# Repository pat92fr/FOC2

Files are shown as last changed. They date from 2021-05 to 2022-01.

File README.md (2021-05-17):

# Development repository for Smart Brushless Servo 

PID/FOC Custom Firmware for B-G431B-ESC1 board.

Follow us on Hackaday.io : https://hackaday.io/project/177578-b-g431b-esc-brushless-servo-controller

## Characteristics

- [x] 16KHz motor PWM 
- [x] Open-loop and closed-loop FOC algorithm (16KHz)
- [x] FOC with CSVPWM algorithm 
- [ ] FOC with Field-Weakening (work in progress)
- [x] Torque and Flux control (P only), with current limiter
- [x] Position control with min/max position limiter (4KHz)
- [x] Velocity control with max velocity limiter (4KHz) 
- [x] Torque and Flux feed-forward
- [x] Auto-calibration of electrical angle and motor rotation 
- [x] USB control interface : dynamixel like protocol allowing full-access to control (RAM) and configuration (EERPOM) 
- [x] CAN control interface : variable-size control frames (RX) and feedback frames (TX), with fail-safe on bus time-out
- [x] Power supply voltage monitoring, with min/max operating voltage (user configurable)
- [x] Position sensor monitoring, with fail-safe on system error and bus time-out
- [x] Temperature monitoring, with fail-safe on maximum temprature (user configurable) 
- [x] GUI Tool for configuration and test

# 1. Hardware (commercial off the shelf)

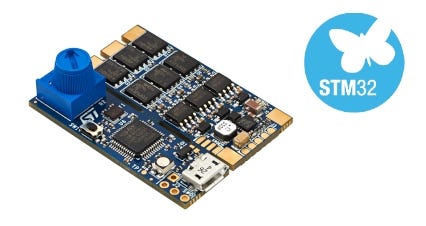
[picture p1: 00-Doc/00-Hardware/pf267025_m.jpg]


Product page : https://www.st.com/en/evaluation-tools/b-g431b-esc1.html

Cost: approx. 18$ per unit.

# 2. Wiring

As mentioned in the user manual, the B-G431B-ESC1 Discovery kit is equipped with a USB connector and different pads for communication, such as:
* U4 USB port for programming and debugging
* J1 for CAN port
* J2 for SWD-STM32F103 (reserved)
* J3 for PWM/UART/BECout input/output signal
* J4 for SWD-STM32G431 debug/programming port (without daughterboard)
* J5/J6 for Lipo battery (30V or 6S max)
* J7 for motor
* J8 for motor sensor (Hall or encoder)

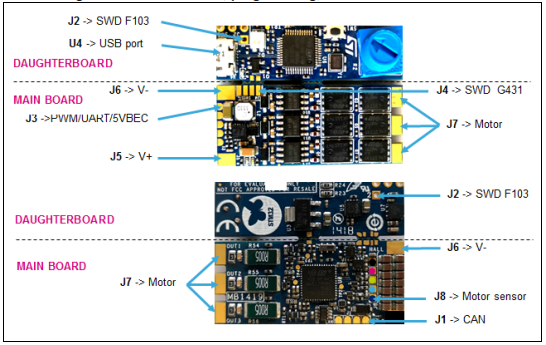
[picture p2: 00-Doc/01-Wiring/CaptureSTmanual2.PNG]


The USB interface is provided on the daughterboard and it allows to program and debug the main board. It provides also the supply voltage to the STM32G431CB MCU in case of no voltage on the bus (J5 and J6 not connected to the LiPo battery).

**For proper operation of the FOC firmware, the J1, J5, J6, J7, an J8 solder pads should be connected.**
The J2, J3, J4 solder pads may be left unconnected.

For J8, the firmware accept two types of position sensor :
* The AS5600 Position Sensor connected through I2C port (https://ams.com/as5600)
* The AS5048A High-Resolution Position Sensor connected through PWM interface (https://ams.com/as5048a)

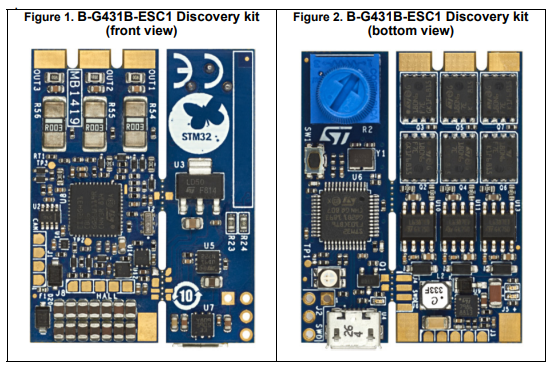
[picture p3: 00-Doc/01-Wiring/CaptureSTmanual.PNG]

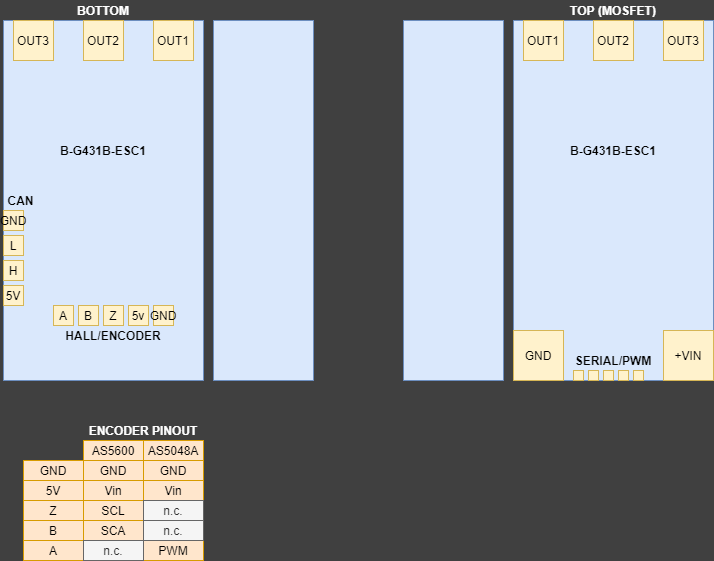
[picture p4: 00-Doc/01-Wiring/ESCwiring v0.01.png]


# 3. Uploading firmware

A full erase of the Chip is strongly recommended, to insure proper initialisation of the default configuration (the last Flash page stores PID/FOC configuration).

The release configuration of the PID/FOC firmware should be built with CubeIDE, and then uploaded using the USB port of the board.

**A hard-coded setting must be adjusted by user, according its hardware configuration :**

At lines 40+ of **main.c**, 
```
// Position sensor type :
//    "AS5600_I2C"
//    "AS5048A_PWM"
#define SENSOR_TYPE AS5048A_PWM
```
# 4. Local user interface

## 4.1. Red STATUS LED

The Red STATUS LED is normally OFF.

When an hardware error occurs, the LED is ON.

User may set the LED ON through USB interface.

## 4.2. Button

A short press on the button starts the calibration sequence. It last a few seconds and the motor turns slowly. Rotor should be free to get a good calibration.

***Notice : The number of pole pairs should be configured before starting the calibration sequence. User may set the pole pairs by connecting the ESC to a computer through USB and running the GUI tool.***

# 5. CAN protocol

The controller accepts CAN frame identifier = 000h + its own ID (user configurable ID).

The controler repies with CAN frame identifier = 010h + its own ID (user configurable ID).

## 5.1. Control frame formats

At ***start-up*** (power-on reset), the controller is in IDLE state (motor brake). The position and velocity set-points, the current feed-forward and the Kp and Kd are reset (=0).

In order to ***arm*** the controller, a full control frame with a 0xFFFFFFFFFFFFFFFF payload should be sent. The velocity set-point, the current feed-forward and the Kp and Kd are reset (=0). The position set-point is set to the present rotor position.

To ***disarm*** the controller, a full control frame with a 0x000000000000000 payload should be send. The position and velocity set-points, the current feed-forward and the Kp and Kd are reset (=0).

The controller ***disarms it-self*** automatically, when a CAN bus time-out occur (no control frame received for one second). The position and velocity set-points, the current feed-forward and the Kp and Kd are reset (=0).

For 16-bit fields, low byte first position, high byte second position.

### 5.1.1. Full control frame

A full control frame has a 64-bit payload.

Field | Length | Value
------------ | ------------- | -------------
Position | 16b | Position set-point in 1/10 degrees
Velocity | 16b | Velocity set-point in degrees per second
Torque | 16b | Torque current feed-forward in mA
Kp | 8b | Position control
Kd | 8b | Velocity control

***Warning : A high value of Kp or Kd may damage the actuator.***

### 5.1.2. Shortened control frames

A 48-bit control frame contains :

Field | Length | Value
------------ | ------------- | -------------
Position | 16b | Position set-point in 1/10 degrees
Velocity | 16b | Velocity set-point in degrees per second
Kp | 8b | Position control
Kd | 8b | Velocity control

A 32-bit control frame contains :

Field | Length | Value
------------ | ------------- | -------------
Position | 16b | Position set-point in 1/10 degrees
Velocity | 16b | Velocity set-point in degrees per second

A 16-bit control frame contains :

Field | Length | Value
------------ | ------------- | -------------
Torque | 16b | Torque current feed-forward in mA

## 5.2. Feedback frame formats

A 32-bit feedback frame contains :

Field | Length | Value
------------ | ------------- | -------------
Position | 16b | Present position in 1/10 degrees
Torque | 16b | Present torque current in mA

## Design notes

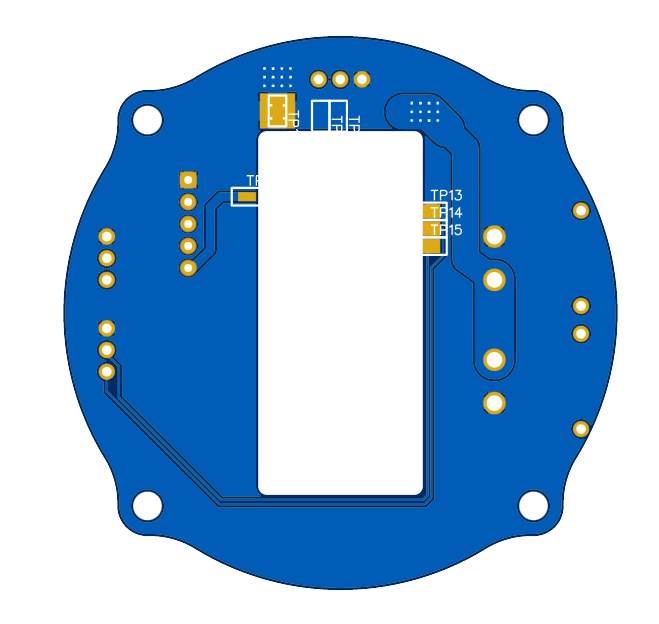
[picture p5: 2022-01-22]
03-Hardware/B-G431B-ESC1/bottom4.PNG

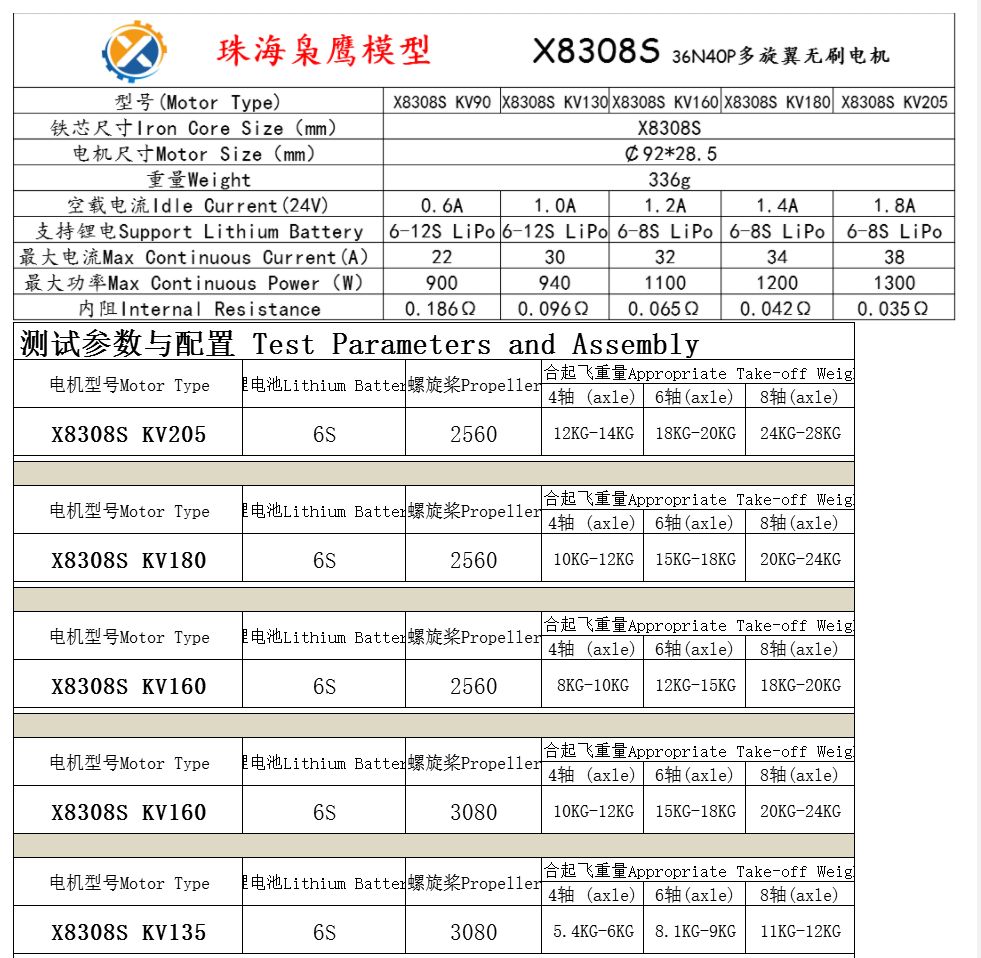
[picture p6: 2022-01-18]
03-Hardware/x8308s/Capture.PNG

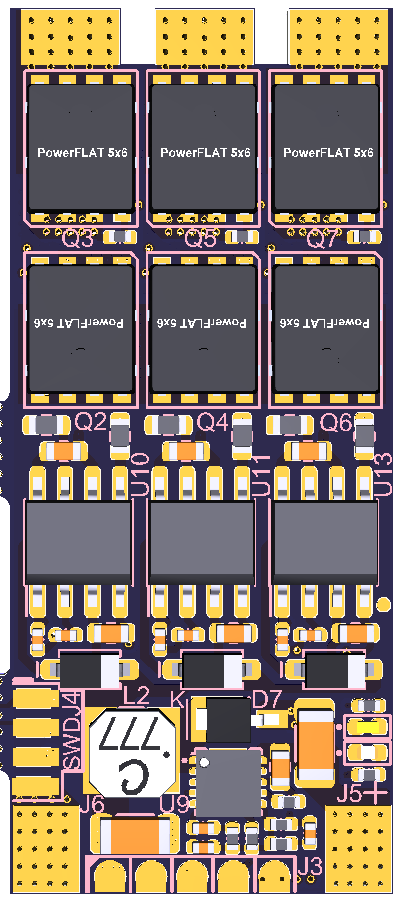
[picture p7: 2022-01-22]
03-Hardware/B-G431B-ESC1/Btop.PNG

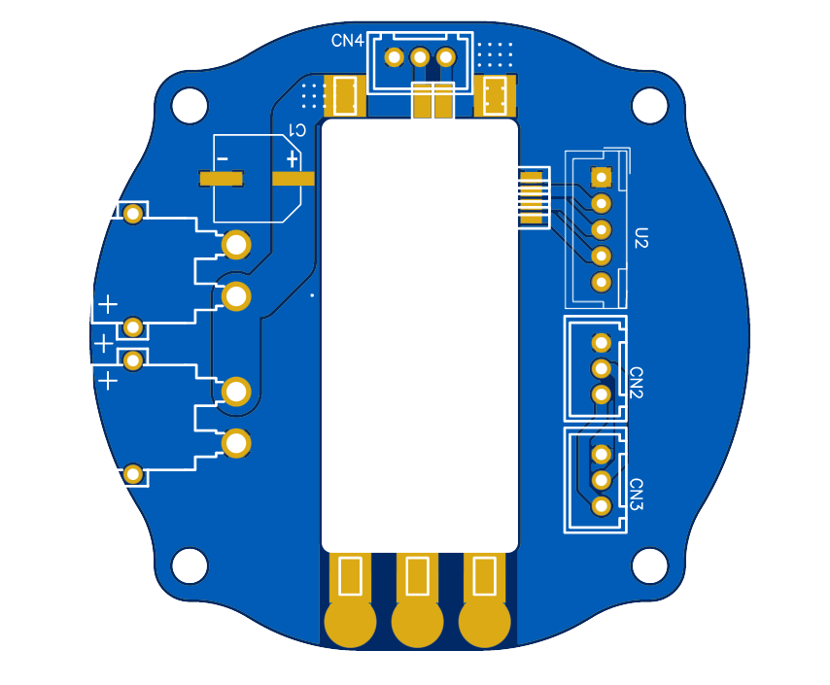
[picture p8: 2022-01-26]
03-Hardware/B-G431B-ESC1/board12.png

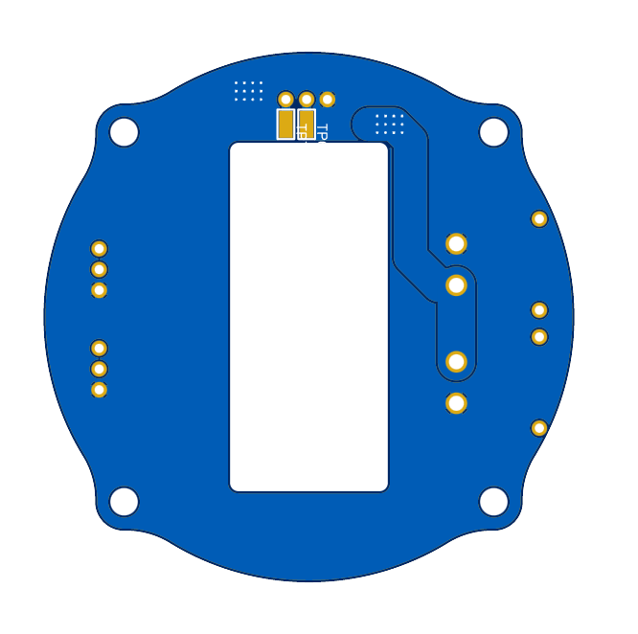
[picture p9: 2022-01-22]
03-Hardware/B-G431B-ESC1/bottom2.PNG

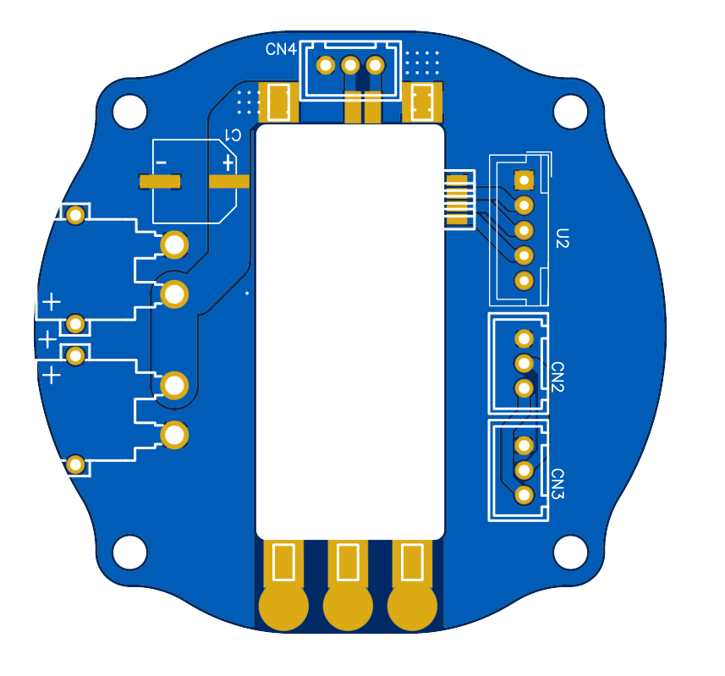
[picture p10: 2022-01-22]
03-Hardware/B-G431B-ESC1/board11.png

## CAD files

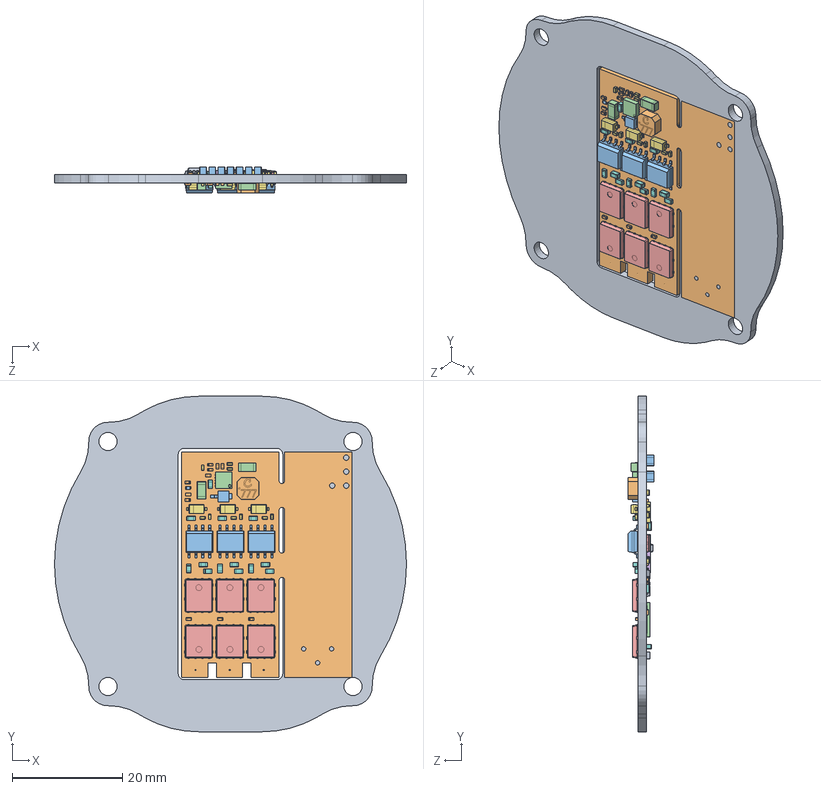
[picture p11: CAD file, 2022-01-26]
03-Hardware/B-G431B-ESC1/Assemblage.SLDASM
64.0 x 61.0 x 4.76 mm
Motherboard
CAPC2012X140 x 14
SON50P300X300X100-11
PowerFLAT_5x6 x 6
INDC1005X55
QFN6 x 2
SON40P120X100X55-6
SOT238
0435.250KRS
User_Library-LED_1006_G_Cut006
User_Library-LED_1006_G_Cut005
User_Library-LED_1006_G_Cut005_(Mirror_#1)
User_Library-LED_1006_G_Pad001
C281-1
C281-2
C281-3
C281-4
C281-5
C281-6
C281-7
SOD123 x 3
CAPC1608X90 x 11
SODFL1608X65 x 10
LPS4018
DO-216AA
CAPC3216X127 x 2
CSTCE
QFN48_7x7
CAPC1005X55 x 28
RESC1608X50 x 9
RESC2012X70 x 3
RESC1005 x 42
SOIC127P600X175 x 3
RESC6330 x 3
pcb_cut

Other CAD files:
03-Hardware/B-G431B-ESC1/C5.sldasm
03-Hardware/B-G431B-ESC1/R63.sldasm
03-Hardware/B-G431B-ESC1/C11.sldasm
03-Hardware/B-G431B-ESC1/D12.sldasm
03-Hardware/B-G431B-ESC1/R11.sldasm
03-Hardware/B-G431B-ESC1/D2.sldasm
03-Hardware/B-G431B-ESC1/Q2.sldasm
03-Hardware/B-G431B-ESC1/R64.sldasm
03-Hardware/B-G431B-ESC1/R23.sldasm
03-Hardware/B-G431B-ESC1/C29.sldasm
03-Hardware/B-G431B-ESC1/R41.sldasm
03-Hardware/B-G431B-ESC1/F1.sldasm
03-Hardware/B-G431B-ESC1/R46.sldasm
03-Hardware/B-G431B-ESC1/C59.sldasm
03-Hardware/B-G431B-ESC1/C54.sldasm
03-Hardware/B-G431B-ESC1/R26.sldasm
03-Hardware/B-G431B-ESC1/C1.sldasm
03-Hardware/B-G431B-ESC1/0435.250KRS.sldprt
03-Hardware/B-G431B-ESC1/3386-T.sldprt
03-Hardware/B-G431B-ESC1/473460001.sldasm
03-Hardware/B-G431B-ESC1/Board.sldasm
03-Hardware/B-G431B-ESC1/C10.sldasm
03-Hardware/B-G431B-ESC1/C13.sldasm
03-Hardware/B-G431B-ESC1/C14.sldasm
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

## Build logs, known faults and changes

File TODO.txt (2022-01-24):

OPCODE PING + 0000000000

OPCODE (ping) returns type of servo ( Front Hip, Rear Hip, Coxa, Hip, Knee)

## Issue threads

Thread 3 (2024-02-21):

AS5600 Encoder Showing Pos_error when ESC Power is connected

samirthegreat, 2024-02-21:
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
When only USB is connected the encoder shows position and loops values within a range.

But when power is connected to the USB:
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

Thxssio, 2024-08-01:
Hello friend, how are you? With this firmware is it possible for me to control a motor to rotate at low speed? I want to control it at low speed and only have speed feedback. I'm trying to use this ESC to control 4 wheels. Basically I want to control an omnidirectional robot.

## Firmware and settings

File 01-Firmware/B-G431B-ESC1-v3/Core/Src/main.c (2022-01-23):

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
/* Includes ------------------------------------------------------------------*/
#include "main.h"

/* USER CODE BEGIN Includes */
#include "serial.h"
#include "position_sensor.h"
#include "foc.h"
#include "pid.h"
#include "math_tool.h"
#include "eeprom.h"
#include "protocol.h"
#include "control_table.h"
#include "binary_tool.h"

/* USER CODE END Includes */

/* USER CODE BEGIN PD */

// CAN Bus termination
#define CAN_BUS_TERMINATION_OFF
#define CAN_BUS_TERMINATION_ON

// Position sensor type :
//    "AS5600_I2C"
//    "AS5048A_PWM"
//#define SENSOR_TYPE AS5048A_PWM
#define SENSOR_TYPE AS5600_I2C

// PID loop period in µs
//  normal setting is 1000us (1KHz)
//  performance setting is 250 (4KHz)
#define PID_LOOP_PERIOD 250

// FOC service loop period in µs
//  normal setting is 10000us (100Hz)
#define SERVICE_LOOP_PERIOD 10000

// Autocalibration at startup
//   uncomment this line for calibrating the ESC/MOTOR at startup
//   comment this line to avoid wearing EEPROM
//#define PERFORM_AUTO_CALIBRATION_AT_STARTUP

// Advanced settings (do not change)
#define ALPHA_VELOCITY				0.24f // (default:0.24) F = 1000Hz ==> Fc (-3dB) = 20Hz

/* USER CODE END PD */

ADC_HandleTypeDef hadc1;
ADC_HandleTypeDef hadc2;
DMA_HandleTypeDef hdma_adc1;
DMA_HandleTypeDef hdma_adc2;

CORDIC_HandleTypeDef hcordic;

FDCAN_HandleTypeDef hfdcan1;

I2C_HandleTypeDef hi2c1;

OPAMP_HandleTypeDef hopamp1;
OPAMP_HandleTypeDef hopamp2;
OPAMP_HandleTypeDef hopamp3;

TIM_HandleTypeDef htim1;
TIM_HandleTypeDef htim4;
TIM_HandleTypeDef htim6;

UART_HandleTypeDef huart2;
DMA_HandleTypeDef hdma_usart2_rx;
DMA_HandleTypeDef hdma_usart2_tx;

/* USER CODE BEGIN PV */

//extern float potentiometer_input_adc;

// serial communication
HAL_Serial_Handler serial;

// CAN communication, state and fail-safe
static FDCAN_RxHeaderTypeDef RxHeader;
static uint8_t RxData[8];
static FDCAN_TxHeaderTypeDef TxHeader;
static uint8_t TxData[8];
bool can_armed = false;
uint32_t can_last_time = 0;

/* USER CODE END PV */

void SystemClock_Config(void);
static void MX_GPIO_Init(void);
static void MX_DMA_Init(void);
static void MX_TIM4_Init(void);
static void MX_USART2_UART_Init(void);
static void MX_TIM1_Init(void);
static void MX_ADC1_Init(void);
static void MX_ADC2_Init(void);
static void MX_OPAMP1_Init(void);
static void MX_OPAMP2_Init(void);
static void MX_OPAMP3_Init(void);
static void MX_CORDIC_Init(void);
static void MX_TIM6_Init(void);
static void MX_FDCAN1_Init(void);
static void MX_I2C1_Init(void);
/* USER CODE BEGIN 0 */

// PWM input capture IT for AS5048A position sensor
void HAL_TIM_IC_CaptureCallback(TIM_HandleTypeDef *htim) __attribute__((section (".ccmram")));

void HAL_TIM_IC_CaptureCallback(TIM_HandleTypeDef *htim)
{
	if (positionSensor_getType() == AS5048A_PWM)
	{
	  API_AS5048A_Position_Sensor_It(htim);
	}
}

// CAN configuration (filters)
static void FDCAN_Config(void)
{
  FDCAN_FilterTypeDef sFilterConfig;

  /* Configure Rx filter */
  sFilterConfig.IdType = FDCAN_STANDARD_ID;
  sFilterConfig.FilterIndex = 0;
  sFilterConfig.FilterType = FDCAN_FILTER_RANGE;
  sFilterConfig.FilterConfig = FDCAN_FILTER_TO_RXFIFO0;
  sFilterConfig.FilterID1 = 0x000;
  sFilterConfig.FilterID2 = 0x100;
  if (HAL_FDCAN_ConfigFilter(&hfdcan1, &sFilterConfig) != HAL_OK)
  {
    Error_Handler();
  }

  /* Configure global filter:
     Filter all remote frames with STD and EXT ID
     Reject non matching frames with STD ID and EXT ID */
  if (HAL_FDCAN_ConfigGlobalFilter(&hfdcan1, FDCAN_REJECT, FDCAN_REJECT, FDCAN_FILTER_REMOTE, FDCAN_FILTER_REMOTE) != HAL_OK)
  {
    Error_Handler();
  }

  HAL_GPIO_WritePin(CAN_SHDN_GPIO_Port, CAN_SHDN_Pin, GPIO_PIN_RESET);
#ifdef CAN_BUS_TERMINATION_ON
  HAL_GPIO_WritePin(CAN_TERM_GPIO_Port, CAN_TERM_Pin, GPIO_PIN_SET); // SET means activating R120 for CAN bus termination
#else
  HAL_GPIO_WritePin(CAN_TERM_GPIO_Port, CAN_TERM_Pin, GPIO_PIN_RESET); // RESET means no bus termination
#endif

  /* Start the FDCAN module */
  if (HAL_FDCAN_Start(&hfdcan1) != HAL_OK)
  {
    Error_Handler();
  }

  if (HAL_FDCAN_ActivateNotification(&hfdcan1, FDCAN_IT_RX_FIFO0_NEW_MESSAGE, 0) != HAL_OK)
  {
    Error_Handler();
  }

  /* Prepare Tx Header */
  TxHeader.Identifier = 0;
  TxHeader.IdType = FDCAN_STANDARD_ID;
  TxHeader.TxFrameType = FDCAN_DATA_FRAME;
  TxHeader.DataLength = FDCAN_DLC_BYTES_8;
  TxHeader.ErrorStateIndicator = FDCAN_ESI_ACTIVE;
  TxHeader.BitRateSwitch = FDCAN_BRS_OFF;
  TxHeader.FDFormat = FDCAN_CLASSIC_CAN;
  TxHeader.TxEventFifoControl = FDCAN_NO_TX_EVENTS;
  TxHeader.MessageMarker = 0;
}

// CAN IT on message receive
void HAL_FDCAN_RxFifo0Callback(FDCAN_HandleTypeDef *hfdcan, uint32_t RxFifo0ITs)
{
  if((RxFifo0ITs & FDCAN_IT_RX_FIFO0_NEW_MESSAGE) != 0)
  {
  	// Handle CAN communication
  	while( HAL_FDCAN_GetRxFifoFillLevel(&hfdcan1,FDCAN_RX_FIFO0)!=0)

    /* Retrieve Rx messages from RX FIFO0 */
    if (HAL_FDCAN_GetRxMessage(hfdcan, FDCAN_RX_FIFO0, &RxHeader, RxData) == HAL_OK)
    {
		// decode message ID=0x000+ID
		if(RxHeader.Identifier==regs[REG_ID]) // message from host controller
		{
		  // can watchdog re-arm
		  if( can_armed )
		  {
			  can_last_time = HAL_GetTick();
		  }
		  uint32_t payload_length = RxHeader.DataLength>>16U;
		  // check payload size = 8
		  if(can_armed && payload_length==2) // Feed Forward Torque only
		  {
			  // TODO Frist BYTE is CODE OP : 0:Torque, 1:VEL 2:POS  N:Is Write M:is Read FF is start of enable

			  // decode payload filed
			  regs[REG_GOAL_TORQUE_CURRENT_MA_L] = RxData[0];
			  regs[REG_GOAL_TORQUE_CURRENT_MA_H] = RxData[1];
			  //HAL_Serial_Print(&serial,"CAN (2)\n");
		  }
		  else if(can_armed && payload_length==3) // Speed, VEL Kp
		  {
			  // decode payload filed
			  regs[REG_GOAL_VELOCITY_DPS_L] = RxData[0];
			  regs[REG_GOAL_VELOCITY_DPS_H] = RxData[1];
			  regs[REG_GOAL_VEL_KP]  = RxData[4];
			  //HAL_Serial_Print(&serial,"CAN (3)\n");
		  }
		  else if(can_armed && payload_length==5) // Position, POS Kp and Kd, VEL Kp
		  {
			  // decode payload filed
			  regs[REG_GOAL_POSITION_DEG_L] = RxData[0];
			  regs[REG_GOAL_POSITION_DEG_H] = RxData[1];
			  regs[REG_GOAL_POS_KP]  = RxData[3];
			  regs[REG_GOAL_POS_KD]  = RxData[4];
			  regs[REG_GOAL_VEL_KP]  = RxData[5];
			  //HAL_Serial_Print(&serial,"CAN (5)\n");
		  }
		  else if(payload_length==8) // position, speed, and torque feed forward, Kp/kd update
		  {
			  if( (RxData[0]==0xFF) && (RxData[1]==0xFF) && (RxData[2]==0xFF) && (RxData[3]==0xFF) &&
				  (RxData[4]==0xFF) && (RxData[5]==0xFF) && (RxData[6]==0xFF) && (RxData[7]==0xFF) )
			  {
				  // init watch dog
				  can_armed = true;
				  can_last_time = HAL_GetTick();
				  regs[REG_TORQUE_ENABLE] = 1;
				  regs[REG_GOAL_POSITION_DEG_L] = 0;
				  regs[REG_GOAL_POSITION_DEG_H] = 0;
				  regs[REG_GOAL_VELOCITY_DPS_L] = 0;
				  regs[REG_GOAL_VELOCITY_DPS_H] = 0;
				  regs[REG_GOAL_TORQUE_CURRENT_MA_L] = 0;
				  regs[REG_GOAL_TORQUE_CURRENT_MA_H] = 0;
				  regs[REG_GOAL_POS_KP]  = 0;
				  regs[REG_GOAL_POS_KD]  = 0;
				  regs[REG_GOAL_VEL_KP]  = 0;
				  //HAL_Serial_Print(&serial,"CAN request ARM\n");
			  }
			  else if(can_armed)
			  {
				  // replace by access read/write to register !


				  // decode payload filed
				  regs[REG_GOAL_POSITION_DEG_L] = RxData[0];
				  regs[REG_GOAL_POSITION_DEG_H] = RxData[1];
				  regs[REG_GOAL_VELOCITY_DPS_L] = RxData[2];
				  regs[REG_GOAL_VELOCITY_DPS_H] = RxData[3];
				  regs[REG_GOAL_TORQUE_CURRENT_MA_L] = RxData[4];
				  regs[REG_GOAL_TORQUE_CURRENT_MA_H] = RxData[5];
				  regs[REG_GOAL_POS_KP]  = RxData[6];
				  regs[REG_GOAL_POS_KD]  = RxData[7];
				  //HAL_Serial_Print(&serial,"CAN (8)\n");
			  }
		  }

		  // then reply by a status frame (shortened)
		  TxHeader.Identifier = 0x10+regs[REG_ID]; // each ESC replies with a message identifier = it is own ID
		  TxHeader.DataLength = FDCAN_DLC_BYTES_4;
		  TxData[0] = regs[REG_PRESENT_POSITION_DEG_L];
		  TxData[1] = regs[REG_PRESENT_POSITION_DEG_H];
		  TxData[2] = regs[REG_PRESENT_TORQUE_CURRENT_MA_L];
		  TxData[3] = regs[REG_PRESENT_TORQUE_CURRENT_MA_H];
		  //TxData[4] = regs[REG_HARDWARE_ERROR_STATUS];
		  //TxData[5] = regs[REG_PRESENT_VOLTAGE];
		  //TxData[6] = regs[REG_PRESENT_TEMPERATURE];
		  //TxData[7] = ....
		  HAL_FDCAN_AddMessageToTxFifoQ(&hfdcan1,&TxHeader,TxData);
		}
    }
  }
}

/* USER CODE END 0 */

/**
  * @brief  The application entry point.
  * @retval int
  */
int main(void)
{
  /* MCU Configuration--------------------------------------------------------*/

  /* Reset of all peripherals, Initializes the Flash interface and the Systick. */
  HAL_Init();

  /* Configure the system clock */
  SystemClock_Config();

  /* Initialize all configured peripherals */
  MX_GPIO_Init();
  MX_DMA_Init();
  MX_TIM4_Init();
  MX_USART2_UART_Init();
  MX_TIM1_Init();
  MX_ADC1_Init();
  MX_ADC2_Init();
  MX_OPAMP1_Init();
  MX_OPAMP2_Init();
  MX_OPAMP3_Init();
  MX_CORDIC_Init();
  MX_TIM6_Init();
  MX_FDCAN1_Init();
  MX_I2C1_Init();
  /* USER CODE BEGIN 2 */
	HAL_TIM_Base_Start(&htim6); // 1us base time
	API_FOC_Init();

  if(eeprom_empty())
	factory_reset_eeprom_regs();
  load_eeprom_regs();
  reset_ram_regs();
  FDCAN_Config();
  positionSensor_init(SENSOR_TYPE);
  positionSensor_update();
  API_FOC_Service_Update();
#ifdef PERFORM_AUTO_CALIBRATION_AT_STARTUP
  API_FOC_Calibrate();
#endif
  HAL_Serial_Init(&huart2,&serial);
//HAL_Serial_Print(&serial,"RESET!\n");

  /* USER CODE END 2 */

  /* Infinite loop */
  /* USER CODE BEGIN WHILE */
  bool torque_was_enable = false;
	uint16_t present_time_us = __HAL_TIM_GET_COUNTER(&htim6);
	uint16_t pid_last_time_us = present_time_us;
	uint16_t service_last_time_us = present_time_us;
	float setpoint_position_deg = 0.0f;
	float setpoint_velocity_dps = 0.0f;
	float setpoint_torque_current_mA = 0.0f;
	float setpoint_flux_current_mA = 0.0f;
	float error_velocity_dps = 0.0f;
	uint32_t pid_counter = 0;
	uint32_t mlp_counter = 0;
	pid_context_t pd_position;
	while (1)
	{
    /* USER CODE END WHILE */

    /* USER CODE BEGIN 3 */

	  	// hardware error clears torque enable register and disable FOC torque controller
		if( regs[REG_HARDWARE_ERROR_STATUS] != 0 )
		{
			// disable torque
			regs[REG_TORQUE_ENABLE] = 0;
			// disable FOC
			API_FOC_Torque_Disable();
			// disarm CAN
			can_armed = false;
		}

		// CAN bus time-out
		// CAN bus watchdog (time-out = 1s hard-coded)
		if( can_armed && (HAL_GetTick()>can_last_time+1000) )
		{
			// disable torque
			regs[REG_TORQUE_ENABLE] = 0;
			// disable FOC
			API_FOC_Torque_Disable();
			// disarm CAN
			can_armed = false;
		}

		// FOC process time-out
		// FOC watchdog (time-out = 10ms hard-coded)
		if( HAL_GetTick() > API_FOC_Get_Timestamp_ms()+10 )
		{
			// error
			regs[REG_HARDWARE_ERROR_STATUS] |= (1 << HW_ERROR_BIT_FOC_TIMEOUT);
			// disable torque
			regs[REG_TORQUE_ENABLE] = 0;
			// disable FOC
			API_FOC_Torque_Disable();
			// disarm CAN
			can_armed = false;
		}

		// 1 to 4Khz low priority process
		present_time_us = __HAL_TIM_GET_COUNTER(&htim6);
		uint16_t const pid_delta_time_us = present_time_us-pid_last_time_us;
		if(pid_delta_time_us>=PID_LOOP_PERIOD)
		{
			pid_last_time_us+=PID_LOOP_PERIOD;
			++pid_counter;

			// update sensor
			positionSensor_update();

			if(regs[REG_TORQUE_ENABLE])
			{
				// transition from torque disable to enable
				if(!torque_was_enable)
				{
					torque_was_enable = true;
					// set goal position to present position to avoid mechanical glicth
					regs[REG_GOAL_POSITION_DEG_L] = LOW_BYTE((int16_t)(10.0f*positionSensor_getDegreeMultiturn()));
					regs[REG_GOAL_POSITION_DEG_H] = HIGH_BYTE((int16_t)(10.0f*positionSensor_getDegreeMultiturn()));
					// reset goal velocity
					regs[REG_GOAL_VELOCITY_DPS_L] = 0;
					regs[REG_GOAL_VELOCITY_DPS_H] = 0;
					// reset feed-forward torque
					regs[REG_GOAL_TORQUE_CURRENT_MA_L] = 0;
					regs[REG_GOAL_TORQUE_CURRENT_MA_H] = 0;
					// reset flux refenrece
					regs[REG_GOAL_FLUX_CURRENT_MA_L] = 0;
					regs[REG_GOAL_FLUX_CURRENT_MA_H] = 0;
					// reset K
					regs[REG_GOAL_POS_KP] = 0;
					regs[REG_GOAL_POS_KD] = 0;
					regs[REG_GOAL_VEL_KP] = 0;
					// reset setpoints
					setpoint_position_deg = 0.0f;
					setpoint_velocity_dps = 0.0f;
					error_velocity_dps = 0.0f;
					// set setpoint_position_deg to avoid glitch
					setpoint_position_deg = positionSensor_getDegreeMultiturn();
					// pid reset
					pid_reset(&pd_position);
					// foc
					API_FOC_Torque_Enable();
				}



				// compute position set-point from goal and EEPROM position limits
				float const goal_position_deg = (float)((int16_t)(MAKE_SHORT(regs[REG_GOAL_POSITION_DEG_L],regs[REG_GOAL_POSITION_DEG_H])))/10.0f;
				float const reg_min_position_deg = (float)((int16_t)(MAKE_SHORT(regs[REG_MIN_POSITION_DEG_L],regs[REG_MIN_POSITION_DEG_H])));
				float const reg_max_position_deg = (float)((int16_t)(MAKE_SHORT(regs[REG_MAX_POSITION_DEG_L],regs[REG_MAX_POSITION_DEG_H])));
				setpoint_position_deg = fconstrain(goal_position_deg,reg_min_position_deg,reg_max_position_deg);
				// compute velocity setpoint from goal and EEPROM velocity limit
				float const goal_velocity_dps = (int16_t)(MAKE_SHORT(regs[REG_GOAL_VELOCITY_DPS_L],regs[REG_GOAL_VELOCITY_DPS_H]));
				float const reg_max_velocity_dps = (int16_t)(MAKE_SHORT(regs[REG_MAX_VELOCITY_DPS_L],regs[REG_MAX_VELOCITY_DPS_H]));
				setpoint_velocity_dps = fconstrain(goal_velocity_dps,-reg_max_velocity_dps,reg_max_velocity_dps);
				// compute torque feed forward
				float const torque_feed_forward_ma = (int16_t)(MAKE_SHORT(regs[REG_GOAL_TORQUE_CURRENT_MA_L],regs[REG_GOAL_TORQUE_CURRENT_MA_H]));
				// compute torque setpoint
				float const error_position_deg = setpoint_position_deg-positionSensor_getDegreeMultiturn();
				float const pos_kp = (float)regs[REG_GOAL_POS_KP]*2.0f;
				float const pos_kd = (float)regs[REG_GOAL_POS_KD]*100.0f*2.0f;
				float const reg_max_current_ma = (uint16_t)(MAKE_SHORT(regs[REG_MAX_CURRENT_MA_L],regs[REG_MAX_CURRENT_MA_H]));
				float const vel_kp = (float)regs[REG_GOAL_VEL_KP]/10.0f;
				error_velocity_dps = ALPHA_VELOCITY*(setpoint_velocity_dps-positionSensor_getVelocityDegree())+(1.0f-ALPHA_VELOCITY)*error_velocity_dps;
				float const reg_reverse = regs[REG_INV_PHASE_MOTOR] == 0 ? 1.0f : -1.0f;
				setpoint_torque_current_mA = reg_reverse*pid_process_antiwindup_clamp_with_ff(
						&pd_position,
						error_position_deg,
						pos_kp,
						0.0f,
						pos_kd,
						reg_max_current_ma,
						0.1f,
						vel_kp*error_velocity_dps+torque_feed_forward_ma
				);
				//setpoint_torque_current_mA=(potentiometer_input_adc/4096)*3000.0f; // DEBUG
				// set flux
				float const goal_flux_current_mA = (int16_t)(MAKE_SHORT(regs[REG_GOAL_FLUX_CURRENT_MA_L],regs[REG_GOAL_FLUX_CURRENT_MA_H]));
				setpoint_flux_current_mA = goal_flux_current_mA;

				// update FOC parameters
				API_FOC_Set_Torque_Flux_Currents_mA(setpoint_torque_current_mA,setpoint_flux_current_mA);

			}
			else // torque disable
			{
				// transition from enable to disable
				if(torque_was_enable)
				{
					torque_was_enable = false;
					// disable FOC
					API_FOC_Torque_Disable();
				}

				// reset unused RAM
				regs[REG_GOAL_POSITION_DEG_L] = 0;
				regs[REG_GOAL_POSITION_DEG_H] = 0;
				regs[REG_GOAL_VELOCITY_DPS_L] = 0;
				regs[REG_GOAL_VELOCITY_DPS_H] = 0;
				regs[REG_GOAL_TORQUE_CURRENT_MA_L] = 0;
				regs[REG_GOAL_TORQUE_CURRENT_MA_H] = 0;
				regs[REG_GOAL_FLUX_CURRENT_MA_L] = 0;
				regs[REG_GOAL_FLUX_CURRENT_MA_H] = 0;
				regs[REG_GOAL_POS_KP] = 0;
				regs[REG_GOAL_POS_KD] = 0;
				regs[REG_GOAL_VEL_KP] = 0;

				// reset all setpoints
				setpoint_position_deg = 0.0f;
				setpoint_velocity_dps = 0.0f;
				error_velocity_dps = 0.0f;

				setpoint_torque_current_mA = 0.0f;
				setpoint_flux_current_mA = 0.0f;
			}

			// RAM Update
			regs[REG_PRESENT_POSITION_DEG_L] = LOW_BYTE((int16_t)(positionSensor_getDegreeMultiturn()*10.0f));
			regs[REG_PRESENT_POSITION_DEG_H] = HIGH_BYTE((int16_t)(positionSensor_getDegreeMultiturn()*10.0f));
			regs[REG_PRESENT_VELOCITY_DPS_L] = LOW_BYTE((int16_t)(positionSensor_getVelocityDegree()*1.0f));
			regs[REG_PRESENT_VELOCITY_DPS_H] = HIGH_BYTE((int16_t)(positionSensor_getVelocityDegree()*1.0f));
			regs[REG_PRESENT_TORQUE_CURRENT_MA_L] = LOW_BYTE((int16_t)(API_FOC_Get_Present_Torque_Current()*1.0f));
			regs[REG_PRESENT_TORQUE_CURRENT_MA_H] = HIGH_BYTE((int16_t)(API_FOC_Get_Present_Torque_Current()*1.0f));
			regs[REG_PRESENT_FLUX_CURRENT_MA_L] = LOW_BYTE((int16_t)(API_FOC_Get_Present_Flux_Current()*1.0f));
			regs[REG_PRESENT_FLUX_CURRENT_MA_H] = HIGH_BYTE((int16_t)(API_FOC_Get_Present_Flux_Current()*1.0f));
			regs[REG_PRESENT_VOLTAGE] = (uint16_t)(API_FOC_Get_Present_Voltage());
			regs[REG_PRESENT_TEMPERATURE] = (uint16_t)(API_FOC_Get_Present_Temp());
			regs[REG_MOVING] = (uint16_t)(fabsf(positionSensor_getVelocityDegree())) > (uint16_t)(regs[REG_MOVING_THRESHOLD_DPS]) ? 1 : 0;

			// DEBUG RAM Update
			regs[REG_SETPOINT_POSITION_DEG_L] = LOW_BYTE((int16_t)(setpoint_position_deg*10.0f));
			regs[REG_SETPOINT_POSITION_DEG_H] = HIGH_BYTE((int16_t)(setpoint_position_deg*10.0f));
			regs[REG_SETPOINT_VELOCITY_DPS_L] = LOW_BYTE((int16_t)(setpoint_velocity_dps*1.0f));
			regs[REG_SETPOINT_VELOCITY_DPS_H] = HIGH_BYTE((int16_t)(setpoint_velocity_dps*1.0f));
			regs[REG_SETPOINT_TORQUE_CURRENT_MA_L] = LOW_BYTE((int16_t)(setpoint_torque_current_mA*1.0f));
			regs[REG_SETPOINT_TORQUE_CURRENT_MA_H] = HIGH_BYTE((int16_t)(setpoint_torque_current_mA*1.0f));
			regs[REG_SETPOINT_FLUX_CURRENT_MA_L] = LOW_BYTE((int16_t)(setpoint_flux_current_mA*1.0f));
			regs[REG_SETPOINT_FLUX_CURRENT_MA_H] = HIGH_BYTE((int16_t)(setpoint_flux_current_mA*1.0f));
			// test new FW
			regs[REG_PROCESSING_TIME] = (uint8_t)(API_FOC_Get_Processing_Time());
			regs[REG_FOC_FREQUENCY] = (uint8_t)(API_FOC_Get_Processing_Frequency()/1000.0f);
			regs[REG_PID_FREQUENCY] = (uint8_t)((float)pid_counter/(float)HAL_GetTick());
			regs[REG_MLP_FREQUENCY] = (uint8_t)((float)mlp_counter/(float)HAL_GetTick());

		} // low priority process 4Khz

		// low priority low frequency
		uint16_t const service_delta_time_us = present_time_us-service_last_time_us;
		if(service_delta_time_us>=SERVICE_LOOP_PERIOD)
		{
			service_last_time_us+=SERVICE_LOOP_PERIOD;

			// FOC service update
			API_FOC_Service_Update();

			// Handle local MMI
			// Led STATUS
			HAL_GPIO_WritePin(STATUS_GPIO_Port,STATUS_Pin,(regs[REG_LED]>0)||(regs[REG_HARDWARE_ERROR_STATUS]>0)?GPIO_PIN_SET:GPIO_PIN_RESET);

			// DEBUG
//			if(potentiometer_input_adc>200)
//				regs[REG_TORQUE_ENABLE] = 1;
//			else
//				regs[REG_TORQUE_ENABLE] = 0;

			// Pressing the button starts calibration
			if(HAL_GPIO_ReadPin(BUTTON_GPIO_Port,BUTTON_Pin)==GPIO_PIN_RESET)
			{
				// disable torque
				regs[REG_TORQUE_ENABLE] = 0;
				// disable FOC
				API_FOC_Torque_Disable();
				// disarm CAN
				can_armed = false;
				// start FOC calibration
				API_FOC_Calibrate();
			}

			// Handle serial communication
			while(HAL_Serial_Available(&serial))
			{
			  char c = HAL_Serial_GetChar(&serial);
			  packet_handler(c);
			}
		} // low priority process very low frequency

		// PERFORMANCE
		//uint16_t t_end = __HAL_TIM_GET_COUNTER(&htim6);
		++mlp_counter;

		// TRACE
		static uint32_t counter = 0;
		if(((++counter)%100)==0)
		{
//			HAL_Serial_Print(&serial,"%d %d\n",
//						//(int)(RADIANS_TO_DEGREES(positionSensor_getRadians())*10.0f),
//						(int)(init_error_data_bits),
//						(int)(RADIANS_TO_DEGREES(present_position_rad)*10.0f)
//						//(int)(RADIANS_TO_DEGREES(expected_position)*10.0f)
//						//(int)(RADIANS_TO_DEGREES(present_velocity_rad)*0.1f)
//						//(int)(RADIANS_TO_DEGREES(theta_rad)*10.0f)
//						//(int)(RADIANS_TO_DEGREES(absolute_position_rad)*10.0f)
//						//regs[REG_PROTOCOL_CRC_FAIL]
//						//(int)(RADIANS_TO_DEGREES(API_AS5048A_Position_Sensor_Get_RPS())*10.0f)
//						//(int)positionSensor_getDeltaTimeEstimation()
//					);


//			HAL_Serial_Print(&serial,"%d %d %d\n",
//						(int)(setpoint_torque_current_mA),
//						(int)(API_FOC_Get_Present_Torque_Current()),
//						(int)(API_FOC_Get_Present_Flux_Current())
//					);

//			HAL_Serial_Print(&serial,"%d\n",
//			(int)API_AS5048A_Position_Sensor_Get_DeltaTimestamp()
//			);
		}


  }
  /* USER CODE END 3 */
}

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


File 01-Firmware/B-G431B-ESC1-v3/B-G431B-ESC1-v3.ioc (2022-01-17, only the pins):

PC6.GPIO_Label=STATUS
PB6.Signal=S_TIM4_CH1
PB2.Signal=OPAMP3_VINM0
PA8.Signal=S_TIM1_CH1
PA0.Signal=ADC1_IN1
PB9.Signal=FDCAN1_TX
PA10.Signal=S_TIM1_CH3
PF1-OSC_OUT.Signal=RCC_OSC_OUT
PC13.Signal=TIM1_CH1N
PC6.Signal=GPIO_Output
PC14-OSC32_IN.Signal=GPIO_Output
PA9.Signal=S_TIM1_CH2
PB14.Signal=ADC1_IN5
PA5.Signal=OPAMP2_VINM0
PB8-BOOT0.Signal=I2C1_SCL
PA11.Signal=FDCAN1_RX
PF0-OSC_IN.Signal=RCC_OSC_IN
PB0.Signal=OPAMP3_VINP
Mcu.UserName=STM32G431CBUx
PC10.Signal=GPIO_Input
PB15.Signal=TIM1_CH3N
PA12.Signal=TIM1_CH2N
PC11.GPIO_Label=CAN_SHDN
PB7.Signal=I2C1_SDA
PC14-OSC32_IN.GPIO_Label=CAN_TERM
PB4.Signal=USART2_RX
PA3.Signal=OPAMP1_VINM0
PC10.GPIO_Label=BUTTON
PC11.Signal=GPIO_Output
PA13.Signal=SYS_JTMS-SWDIO
PA1.Signal=OPAMP1_VINP
PB3.Signal=USART2_TX
PA14.Signal=SYS_JTCK-SWCLK
PB12.Signal=ADC1_IN11
PA7.Signal=OPAMP2_VINP

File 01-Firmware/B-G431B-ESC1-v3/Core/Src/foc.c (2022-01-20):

/*
 * foc.c
 *
 *  Created on: 16 janv. 2021
 *      Author: Patrick, Kai
 */

/// DOC FOC(open loop) : https://docs.simplefoc.com/foc_theory
/// DOC SVM https://www.embedded.com/painless-mcu-implementation-of-space-vector-modulation-for-electric-motor-systems/

#include "foc.h"
#include "foc_utils.h"
#include "cordic.h"
#include "serial.h"
#include "position_sensor.h"
#include "math_tool.h"
#include "control_table.h"
#include "binary_tool.h"
#include "pid.h"

#include <string.h>
#include <math.h>

// hard-coded settings
#define ALPHA_CURRENT_SENSE_OFFSET	0.001f 	// low pass filter for calibrating the phase current ADC offset (automatically)

// FOC peripherals
extern TIM_HandleTypeDef htim1;
extern TIM_HandleTypeDef htim4;
extern TIM_HandleTypeDef htim6;
extern ADC_HandleTypeDef hadc1;
extern ADC_HandleTypeDef hadc2;
extern OPAMP_HandleTypeDef hopamp1;
extern OPAMP_HandleTypeDef hopamp2;
extern OPAMP_HandleTypeDef hopamp3;

// serial communication (UART2) for TRACEs
// TODO : use STM32 CUBE MONITOR
extern HAL_Serial_Handler serial;

// high priority high interupt
// TIM1 => Update Event Trigger => CAN (x2) ==> DMA (x2) ==> FOC IT
void API_FOC_It(ADC_HandleTypeDef *hadc) __attribute__((section (".ccmram")));

// high priority high frequency process called by IT
void API_FOC_Torque_Update()  __attribute__((section (".ccmram")));

// ADC IT for motor current sense, and votlage/temperature monitoring
void HAL_ADC_ConvCpltCallback(ADC_HandleTypeDef *hadc) __attribute__((section (".ccmram")));

void HAL_ADC_ConvCpltCallback(ADC_HandleTypeDef *hadc)
{
	API_FOC_It(hadc);
}

// FOC state variable
#define FOC_STATE_IDLE 0 					// brake
#define FOC_STATE_TORQUE_CONTROL 1 			// normal operation
#define FOC_STATE_FLUX_CONTROL 10 			// calibration
static uint32_t foc_state = FOC_STATE_IDLE;
static uint16_t foc_timestamp_us = 0;
static uint32_t foc_timestamp_ms = 0;

// FOC setpoints variables
static float setpoint_torque_current_mA = 0.0f;
static float setpoint_flux_current_mA = 0.0f;
static float setpoint_electrical_angle_rad = 0.0f;
static float setpoint_flux_voltage_V = 0.0f;

// FOC variables
static float present_Ids_mA = 0.0;
static float present_Iqs_mA = 0.0f;
static pid_context_t flux_pi;
static pid_context_t torque_pi;

// FOC current sense
static float motor_current_mA[3] = {0.0f,0.0f,0.0f};
static float motor_current_input_adc_offset[3] = {2464.0f,2482.0f,2485.0f};
static float const motor_current_input_adc_KmA = -29.41f; // V/mA // note : the (-) sign here
// process phase current
// Note : when current flows inward phase, shunt voltage is negative
// Note : when current flows outward phase, shunt voltage is positive
// Note : The current sign is positive when flowing in to a phase
// Note : The current sign is negative when flowing out from a phase

// FOC analog measure
static int32_t current_samples = 0;
volatile uint16_t ADC1_DMA[5] = { 0,0,0,0,0 }; 	// Dummy conversion (ST workaround for -x),
volatile uint16_t ADC2_DMA[3] = { 0,0,0 }; 		// Dummy conversion (ST workaround for -x)
static float motor_current_input_adc[3] = {0.0f,0.0f,0.0f};
float potentiometer_input_adc = 0.0f; // public
static float vbus_input_adc = 0.0f;
static float temperature_input_adc = 0.0f;
static float present_voltage_V = 0.0f;
static float present_temperature_C = 0.0f;

// FOC performance monitoring
static float average_processing_time_us = 0.0f;
static uint32_t foc_counter = 0;

void API_FOC_Torque_Enable()
{
	foc_state = FOC_STATE_TORQUE_CONTROL;

	setpoint_torque_current_mA = 0.0f;
	setpoint_flux_current_mA = 0.0f;
    setpoint_electrical_angle_rad = 0.0f;
    setpoint_flux_voltage_V = 0.0f;

    present_Ids_mA = 0.0f;
    present_Iqs_mA = 0.0f;

	pid_reset(&flux_pi);
	pid_reset(&torque_pi);
}

void API_FOC_Torque_Disable()
{
	foc_state = FOC_STATE_IDLE;
	HAL_Delay(1);

	// enforce brake
	LL_FOC_brake();
}

void API_FOC_Set_Torque_Flux_Currents_mA(float Iq_mA, float Id_mA)
{
	setpoint_torque_current_mA = Iq_mA;
	setpoint_flux_current_mA = Id_mA;
}

// user API function
// this function reset state of FOC
// This function starts peripherals
void API_FOC_Init()
{
	// Motor PWM init and BRAKE
	__HAL_TIM_SET_COMPARE(&htim1,TIM_CHANNEL_1,0);
	__HAL_TIM_SET_COMPARE(&htim1,TIM_CHANNEL_2,0);
	__HAL_TIM_SET_COMPARE(&htim1,TIM_CHANNEL_3,0);
	HAL_TIM_PWM_Start(&htim1,TIM_CHANNEL_1);
	HAL_TIMEx_PWMN_Start(&htim1,TIM_CHANNEL_1) ;
	HAL_TIM_PWM_Start(&htim1,TIM_CHANNEL_2);
	HAL_TIMEx_PWMN_Start(&htim1,TIM_CHANNEL_2) ;
	HAL_TIM_PWM_Start(&htim1,TIM_CHANNEL_3);
	HAL_TIMEx_PWMN_Start(&htim1,TIM_CHANNEL_3) ;
	// OPAMP and ADC init
	HAL_OPAMP_Start(&hopamp1);
	HAL_OPAMP_Start(&hopamp2);
	HAL_OPAMP_Start(&hopamp3);
	HAL_ADC_Start_DMA(&hadc1,(uint32_t*)ADC1_DMA,5);
	HAL_ADC_Start_DMA(&hadc2,(uint32_t*)ADC2_DMA,3);
	// CORDIC init
	API_CORDIC_Processor_Init();
	// disable FOC
	API_FOC_Torque_Disable();
}

void LL_FOC_Update_Temperature() __attribute__((section (".ccmram")));

// low level function
// this function update present_temperature_C
// this function update REG_HARDWARE_ERROR_STATUS register (set/reset HW_ERROR_BIT_OVERHEATING bit)
// this function use REG_TEMPERATURE_LIMIT register
// the temperature ADC samples are collected with phase current samples
void LL_FOC_Update_Temperature()
{
	// convert ADC sample into temperature (STM32G431-ESC1 specific)
	static float const R60 = 4700.0f; // ohm
	static float const eps = 0.1f; // epsilon (avoid divide by zero)
	float const R_NTC = R60*(4096.0f/(temperature_input_adc+eps)-1.0f); // 10kohm NTC at 25°C
	static float const Beta = 3455.0f; // for a 10k NTC
	static float const Kelvin = 273.15f; //°C
	static float const T0 = 273.15f + 25.0f;
	static float const R0 = 10000.0f; // 10kohm at 25° for 10k NTC
	float const present_temperature_K = Beta * T0 / ( Beta - T0*logf(R0/R_NTC) );
	present_temperature_C = present_temperature_K-Kelvin;

	// apply thermal protection and update hardware error register
	float const max_temperature_C = regs[REG_TEMPERATURE_LIMIT];
	if(present_temperature_C>max_temperature_C)
	{
		// set overheating error
		regs[REG_HARDWARE_ERROR_STATUS] |= 1UL << HW_ERROR_BIT_OVERHEATING;
		//HAL_Serial_Print(&serial,"h");
	}
	else if( ((regs[REG_HARDWARE_ERROR_STATUS]&(1UL << HW_ERROR_BIT_OVERHEATING))!=0) ) // hard-coded hysteresis 12°C
	{
		if(present_temperature_C<max_temperature_C-12.0f)
			// clear overheating error
			regs[REG_HARDWARE_ERROR_STATUS] &= ~(1UL << HW_ERROR_BIT_OVERHEATING);
		// wait for cooling
	}
	else
	{
		// clear overheating error
		regs[REG_HARDWARE_ERROR_STATUS] &= ~(1UL << HW_ERROR_BIT_OVERHEATING);
	}

}

void LL_FOC_Update_Voltage() __attribute__((section (".ccmram")));
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

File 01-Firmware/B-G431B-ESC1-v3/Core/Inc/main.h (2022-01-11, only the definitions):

#define CAN_TERM_Pin GPIO_PIN_14
#define CAN_TERM_GPIO_Port GPIOC
#define STATUS_Pin GPIO_PIN_6
#define STATUS_GPIO_Port GPIOC
#define BUTTON_Pin GPIO_PIN_10
#define BUTTON_GPIO_Port GPIOC
#define CAN_SHDN_Pin GPIO_PIN_11
#define CAN_SHDN_GPIO_Port GPIOC

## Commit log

2021-03-29 regenerating HAL source code files from merged ioc
    I2C timing updated
2021-05-16 FOC and PID frequency statistics
2021-05-16 better sensor type coding
2021-05-16 calibration starts when button pressed
2021-05-17 Fix VdVq norm and present voltage maximum
    [foc.c]
2021-05-17 Support of STATUS LED (user controlable)
2021-05-17 STATUS LED coupled with Hardware Alarms
2021-05-17 fixing periodic hardware error with position sensor
    position sensor may be update during FOC algorithm execution. that cause bad computation of position sensor time out (10x per second).
    [as5048a.c, control_table.h, eeprom_frame.py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]
2021-05-18 need for speed
    DMA continous request, faster ADC IT
    40KHz TIM1 (20KHz motor PWM)
    Better main loop, running at 20KHz with AS5048A
    Main loop at +40KHz.
2021-05-18 CCM RAM rebuild
    Maximum performance with a small reserve
    22KHz FOC
    4Kh PID
    100KHz main loop
2021-05-18 Cal Current sense rollback & Table cleanup
2021-05-18 Current CAL update
2022-01-13 up ok both motors without fw
2022-01-13 up Iq Id filtering not usefull
2022-01-15 up change FOC called from ADC DMA It (risk)
2022-01-15 up (velocity glitch)
2022-01-15 up fixing position estimation
    [as5048a.c, control_table.h, foc.c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]
2022-01-15 up glitch not fixed
    [ClasseurPositionEstimation.xlsx]
2022-01-15 up fixing glitch position
    [ClasseurPositionEstimation.xlsx]
2022-01-16 up fixing position estimation (almost done)
    AS5048A bug around ZERO at high speed
    [ClasseurPositionEstimation.xlsx]
2022-01-16 up position sensor fixed
    [as5048a.c, main.c]
2022-01-16 up clean up after fix position estimation
    [as5048a.c, control_table.h, eeprom_frame.py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]

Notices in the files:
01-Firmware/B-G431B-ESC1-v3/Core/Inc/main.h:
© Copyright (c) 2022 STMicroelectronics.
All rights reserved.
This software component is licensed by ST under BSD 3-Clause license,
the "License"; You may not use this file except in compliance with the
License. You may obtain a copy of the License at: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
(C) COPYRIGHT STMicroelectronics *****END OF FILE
